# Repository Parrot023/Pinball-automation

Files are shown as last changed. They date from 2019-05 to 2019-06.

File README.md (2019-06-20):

# Pinball automation

This project is about turning an old classic pinball machince, into an automatic pinball beast. It's done by ball detecting sensors
above the flippers, and an Arduino (Nano) activating the flippers via relays.

## Usefull information

### 3D print info:

**Sensor holder**

- Body depth: 10 mm.
- Body height: 7 mm.
- Body lenght: is defined by number number of repeats.

- Divider (the wall between each sensor): 3 mm.

- Screw hole size: 3 mm.

- Cut out length (for sensor): 11 mm.
- Cut out height (for sensor): 5 mm.

### Notes

- The atmega chips only supports internal pull up resistors not pull down

- Diodes used: 1N914

- Arduino used: Arduino nano

- Sensors used: TCRT5000 Module

## To do

- ~~Put pull down resistor on multi sensor board~~
- Find a solution so that you dont accidentally place sensor incorrectly
into multi sensor board
- Find a solution to the sensors activating each other
- Try out other IR senors (Maybe they are rated for longer distances)
- Add OpenScad files for sensor tube
- Make another multi sensor board. With only 4 sensors.
- Make the other side of the pinball machine automatic.

## Log:

### June 20th

- Started on the second multi sensor board. this time only with 4 sensors
with more space between them (3-8 mm). We have found this to be the best
solution.
- Finished the second multi sensor board.
- Build a piece of tree to hold the other sensor board on the flipper machine
- Modified src/pinball.ino to work with both the left and rigth flipper.
this functinality has been there before, but during testing only the right
flipper was active in the src code.
- Tested it out to see it works (It does)
- It could be upgraded, but only using 8 sensors todays results were perfect
the sensors saved the ball about 11 times at max.
- Finished the project and packed it town.
- In the future this project will probably not be updated. Cause we will
be working on other things. I will though probably upload some images of the 
circuits, a photo and a video of the pinball beast operating in the future
- Walked off into the summer sun with the great sattisfaction of having 
worked on this project for a long time and seing it working and calling it
done (for now)

### June 6th

- Printed out 5 more sensor tubes.
- We decided to stick with 4 sensors on one side. To avoid a problem where
the sensors get stuck. These sensor have sensor tubes on them.
- We got it working with 4 sensors on the board. 
**Important**
These 4 sensor work better with sensor tubes on them.

**PROBLEM:**
- We could not make 7 sensor work together. They keep activating each other
We think the cause can be something called hysteresis (google hysteresis
comparator if you dont know what it is).

### May 16th

- Printed 2 sensor tubes (sensor tubes are small rectangular 3d printed objects
which sit on the sensors led module. The goal of the tube is to prevent light
from one sensor reaching another).
OpenScad files for the sensor tubes are coming soon.

- Cut out a new piece of tree to hold the multi sensor board on the
pinball machine and drilled holds for the multi sensor board.
- Added Line sensor (Model number: TCRT5000) datasheet to link to README
- [TCRT5000 Datasheet](https://www.vishay.com/docs/83760/tcrt5000.pdf)

- Added image of line sensor to repo 

**PROBLEM:**
- We found the sensor activating each while testing it on pinball
we are working on a 3D printed object that blocks the light from one sensor
reaching another sensor on the multi sensor board.
- Tobias found the datasheet for the line sensors.
  - The sensors are rated for a distance between 0.2 mm - 15 mm.
  - Their peak distance is 2.5 mm.
  - Our sensors are 33 mm from the playfield of the pinball machine

### May 9th

- Finished multi sensor board
- Put pull down resistor on multi sensor board
- multi sensor board is now fully functional
- We had a problem with the multi sensor board but it was due to a loose connection
- Openscad files for sensor holder and breadboard holder were added to the repository

### May 2nd

- Almost done with multi sensor board
- No problems

### April 25th

- Single sensor works.

**PROBLEMS:**

- Tobias ruined one of the sensors by placing it incorrectly in the multi sensor board. This problem needs to be solved.
- Multi sensor board with diodes dosnt work (Symptom: swithes on and off relay when sensor is not active).

**SOLVED:**

- The multi sensor board now works. We concluded that a pull down resistor is needed, the problem did not occure with just one sensor because,
with only one sensor there were no diode in the way. with the diodes, when no power was coming from the sensor output, the pin was just floating
- We still need to find a solution so that you dont accidentally place the sensor into the multi sensor board incorrectly

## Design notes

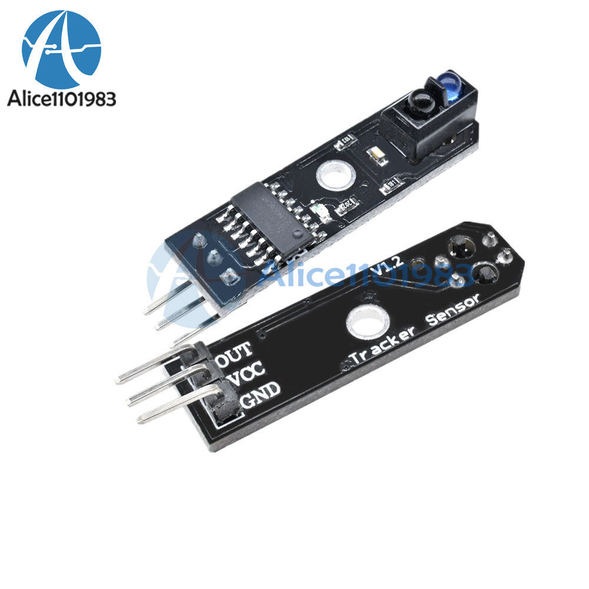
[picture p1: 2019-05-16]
TCRT5000.jpg

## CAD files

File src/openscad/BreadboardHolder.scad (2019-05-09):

//Messurements

//Breadboard height
bbh = 9.1;

//Thickness of holder
wall = 3;

//Margin of error for screw
marg = 0.2;

//Faces of circles
faces = 100;


// Round corners and main cube
difference(){    
    
    //Make main cube
    difference(){ 
        translate([0, 0, (bbh+wall)/2-(wall/2)]){
            cube(bbh+wall, center=true);
        }
        // Corner cut out (For rounded corner)
        translate([-bbh/2, -bbh/2, bbh/2])
            cube([wall,wall,wall*10], center=true); 
    }
    
    //Cuts out where breadboard should be
    translate([-wall/2,-wall/2, wall]) cube(bbh, center=true);
}

// Circle for rounded corner
translate([-bbh/2+wall/2, -bbh/2+wall/2, bbh])
        cylinder(wall, r=wall, center=true, $fn=faces);

//Surround circles.
difference() {
    hull() {
        
        //Shape used for hulling
        cube([bbh+wall, bbh+wall, wall], center=true);
        
        //Circle 1
        translate([bbh+wall, 0, 0]) 
            cylinder(wall, d=bbh+wall, center=true,$fn=faces);
        
        //Circle 2
        translate([0, bbh+wall, 0]) 
            cylinder(wall, d=bbh+wall, center=true,$fn=faces);
    }

 

    //Cuts out where breadboard should be because otherwise big plate in bottom
    translate([-wall/2,-wall/2,-wall/2]) cube(bbh, center=true);
    
    //Make screw holes
    translate([bbh+wall/2,0,0]) cylinder(20, d=3+marg, center=true, $fn=faces);
    translate([0,bbh+wall/2,0]) cylinder(20, d=3+marg, center=true, $fn=faces);
}

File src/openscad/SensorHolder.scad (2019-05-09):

//Body messurements
depth = 10;
height = 7;

//Cutout messurements
cutout_length = 11;
cutout_height = 5;

//Divider messurements
divider = 3;

//Screwhole size
hole_size = 3;

//Cylinder faces
faces = 50;

//How many sensors?
repeat = 5;

//Spacing distance for cylinder to make code shorter in length
space = divider+cutout_length;

//Calculates length of body and assigns value to variable length
length = ((divider+cutout_length)*repeat)+divider;

difference() {
    //Make body
    cube([repeat*cutout_length+(repeat+1)*divider,depth,height]);
    
    //Make cutouts and screw holes
    for (i = [1 : repeat]) {
        
        //Cutouts
        translate([(divider*i)+(cutout_length*(i-1)),0,0])
            cube([cutout_length,depth,cutout_height]);
            
        //Screw holes
        translate([space*i-cutout_length/2, depth/2, cutout_height])
            cylinder(h=height-cutout_height, d=hole_size, $fn=faces);
    }
}

//Make handles
handle_offset = 5;

/*
//Handle 1
translate([handle_offset*-1, 0, cutout_height])
    cube([handle_offset, depth, height-cutout_height]);

translate([handle_offset*-1, depth/2, cutout_height])
    cylinder(h=height-cutout_height, r=depth/2, $fn=faces);

//Handle 2
translate([length, 0, cutout_height])
    cube([handle_offset, depth, height-cutout_height]);

translate([length+handle_offset, depth/2, cutout_height])
    cylinder(h=height-cutout_height, r=depth/2, $fn=faces);
*/

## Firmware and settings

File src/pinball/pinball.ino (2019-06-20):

//A wonderfull program by Andreas J.
//the goal is to read the output from a sensor and activate a releay

//delays
const int flipperUpTime = 100;
const int flipperWaitTime = 500;

//sensor pins
const int rightsensor = 2;
const int leftsensor = 3;

//counting every time the sensors are activated
int count = 0;
int prev_count;

//flipper pins
const int rightflipper = 4;
const int leftflipper = 5;




void setup() { //------------------------------------------------------------------------------------------------------------>

  //declare pin modes
  pinMode(rightsensor, INPUT);
  pinMode(rightflipper, OUTPUT);

  pinMode(leftsensor, INPUT);
  pinMode(leftflipper, OUTPUT);

  digitalWrite(rightsensor, LOW);
  digitalWrite(leftsensor, LOW);

  //starts the serial communication
  Serial.begin(9600);

}

void loop() { //--------------------------------------------------------------------------------------------------------------->

  if (prev_count != count) {
    Serial.println(count);
    prev_count = count;
  }


  //right flipper ------------------------------------------------------------------------------->
    Serial.println(digitalRead(rightsensor));
    if (digitalRead(rightsensor) == HIGH) {
        
      Serial.println(digitalRead("ACTIVE"));
      //activate flipper
      digitalWrite(rightflipper, HIGH);

      //this delay is needed by the flipper, if this delay wasnt here the flipper would not flip
      delay(flipperUpTime);

      //deactivate flipper
      digitalWrite(rightflipper, LOW);

      //delay to prevent the flipper from activating itself,
      //this might have to be redone in the future for support for multiple sensors per flipper
      //maybe using interrupts again
      delay(flipperWaitTime);

      //counts number of sensor activations
      count ++;
  }

  //right flipper ------------------------------------------------------------------------------->
    Serial.println(digitalRead(leftsensor));
    if (digitalRead(leftsensor) == HIGH) {
        
      Serial.println(digitalRead("ACTIVE"));
      //activate flipper
      digitalWrite(leftflipper, HIGH);

      //this delay is needed by the flipper, if this delay wasnt here the flipper would not flip
      delay(flipperUpTime);

      //deactivate flipper
      digitalWrite(leftflipper, LOW);

      //delay to prevent the flipper from activating itself,
      //this might have to be redone in the future for support for multiple sensors per flipper
      //maybe using interrupts again
      delay(flipperWaitTime);

      //counts number of sensor activations
      count ++;
  }

} //end of main loop ----------------------------------------------------------------------------------------------------------->

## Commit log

2018-10-11 created sketch folder for arduino code, improved code for use with flipper arms and added comments
2018-10-14 Deleted FlipperMacineProject.ino from this location and moved it in an arduino project folder
2019-03-21 Rearranged folders and renamed 'flipper' to 'pinball'
    [pinball.ino]
2019-03-28 Renamed src dir for arduino sdk compatability
2019-05-09 Added openscad files for breadboard holder and sensor holder
    [BreadboardHolder.scad, SensorHolder.scad]
2019-05-16 Added jpg of line sensor
2019-06-20 Added controle of the left flipper to src/pinball/pinball.ino and updated log
    [pinball.ino]
